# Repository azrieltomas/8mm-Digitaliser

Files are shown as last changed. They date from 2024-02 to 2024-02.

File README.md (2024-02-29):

# 8mm-Digitaliser
Hardware and software designs for the worlds worst 8mm film scanner

After finding a reel of 8mm film I set out to try to digitise it. A quick attempt with my Epson v850 showed this was not a viable option, and a stubborn refusal to look online at anyone else's attempt (for a while) led to this.

The basic design concept is to advance the film reel frame by frame, as close as possible to exactly, and photograph each frame with a digital camera.

This project consists of four parts:
* 3D printed parts for advancing the film
* Arduino microcontroller to control the stepper motor and camera
* Python script to align the images
* A few other shortcuts to turn it into a video

### Film Holder and Advancer
This is a series of 3D printed parts to hold the film in place and advance it past a lamp. To save time, I designed it without a base, and bolted each piece to a wooden board. Parts requiring a bit of accuracy were printed with a base. Partially inspired by the operation of a cassette, the film is advanced by a single sprocket, and rests on a series of rollers (or just plastic cylinders to aid alignment and tension).

The single driving sprocket was designed around the stepper motor used (a cheap-ish Jaycar YM2754 I've had sitting around for years), which steps 7.5 degrees with each movement. Given that 8mm film perforations are spaced 3.81 mm apart, the radius of the sprocket needs to be 29.106 mm. While the printer may not achieve this accuracy, the hope is any deviation causes a constant shift that can be countered later when cropping the photos.

For a lamp I used a battery powered LED lamp designed to be fitted to a camera horseshoe as kind of not-quite-ring lamp.

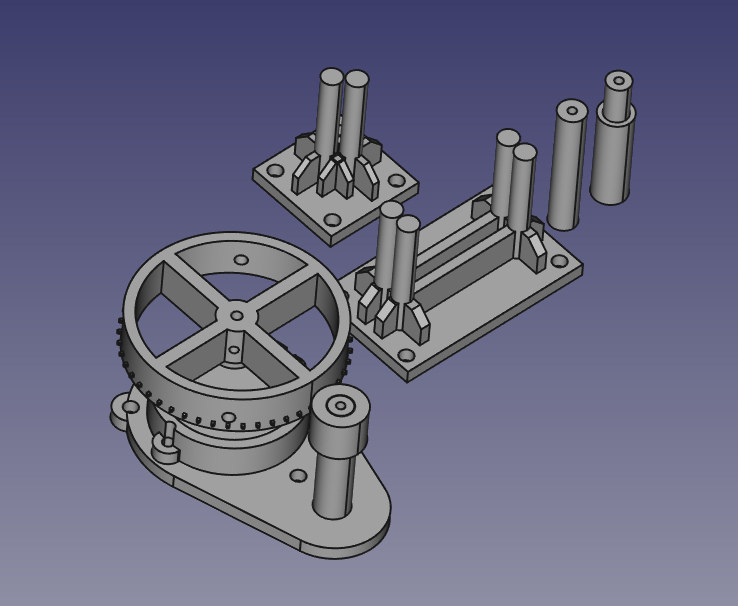
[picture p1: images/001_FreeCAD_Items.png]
3D Parts
\
*3D Parts in FreeCAD*

### Stepping and Photographing
The camera used is a Canon 200D MkII, fitted with a macro adaptor and 200 mm lens, but any camera with an external trigger and suitably powerful lens could be used.

The stepper control has four buttons: step forward, step backward, run continuously, halt. After stepping the motor, the system waits for a 250 ms for everything to settle, fires the shutter, waits 500 ms for the shutter to finish, and then another 500 ms for cooling. This last part is imperative when using 3D printed parts - the stepper motor when stopped (but enabled) dissipates 12W of heat which soon starts softening the driving sprocket and causing it to slip. Giving it half a second to cool by disabling it solves the heat problems, and keeps the noise of the bench power supply down.

The camera's trigger socket is only a 2.5 mm TRS connection:
* Tip: Shutter
* Ring: Focus
* Sleeve: Ground

By shorting T or R to S the camera will activate this function. With S connected to ground, T is "shorted" by enabling a 74HC126 tri-state buffer output. Otherwise the buffer is disabled and output in Hi-Z mode. Alternatively a 5V relay can be used.

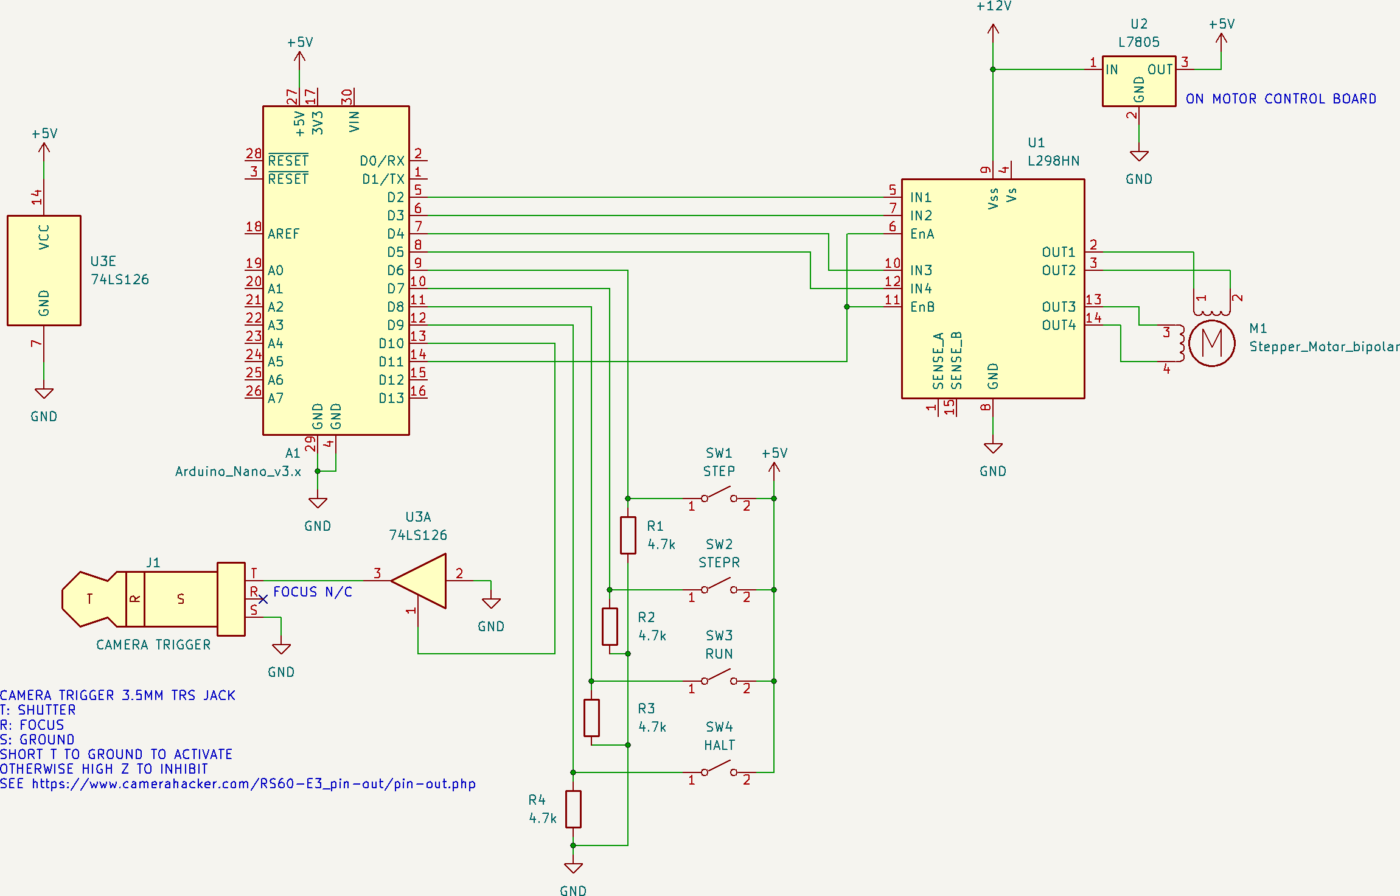
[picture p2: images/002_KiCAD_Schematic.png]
Circuit Design
\
*Circuit Design in KiCAD*

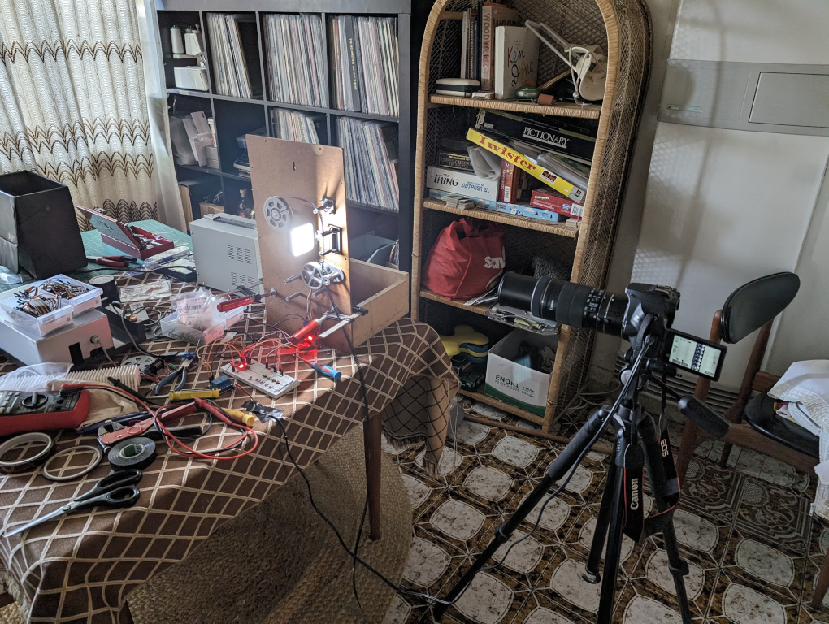
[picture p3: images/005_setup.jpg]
A mess
\
*Physical setup, experiencing continuous modification & improvement*

### Aligning Photographs
Prior to alignment, the photographs need to be cropped appropriately. I've done this either in Lightroom very quickly or by using ImageMagick (choosing a rough image size and start position):
```
for f in *.tif; do convert -crop (resx)x(resy)+(xpos)+(ypos) +repage $f crop_$f; done
```

This scanning system has a lot of bounce and shift. In an attempt to smooth it out, I tried the following to align the images:
* Hugin image stitcher (didn't really work)
* ImageJ / Fiji (didn't really work)
* Photoshop auto-align (awful results)
* Vidstab (decent results, but frame tracking starts to shift like a bad VCR)

The problem with the image programs is they're attempting to align the images in the 8mm frame, not the frame itself. For a moving camera film this is obviously not what we want.

After trying these I sought a better solution and came upon [cpixip's Super-8 detector](https://github.com/cpixip/sprocket_detection). This was a fantastic program and I could not thank them enough for their hard work (check out [their profile on Kinograph.cc](https://forums.kinograph.cc/u/cpixip/summary)), but a couple differences between Super-8 and 8mm meant this required some modification:
* Super-8 perforations are aligned with the centre of the image, 8mm is aligned with the top and bottom, meaning there are two holes per image (or rather, two halves)
* The 8mm film I have has Kodak lettering along the edge, which throws the detector at times

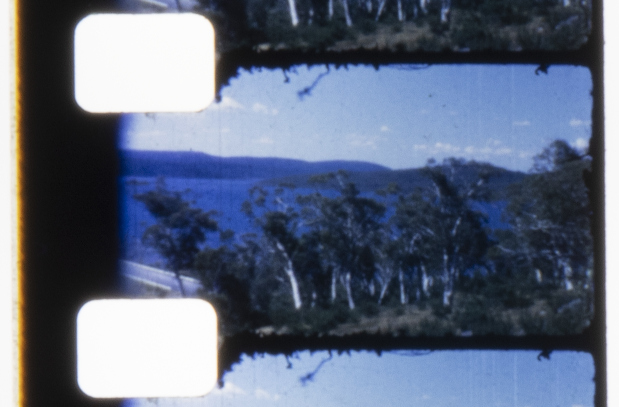
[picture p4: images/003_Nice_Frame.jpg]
A nice frame
\
*An easy frame to analyse*

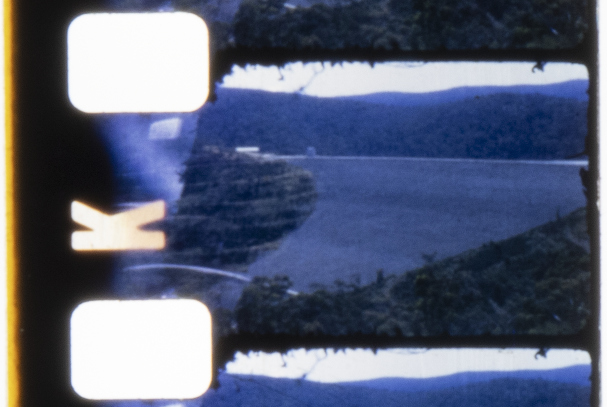
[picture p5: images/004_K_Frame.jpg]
An annoying frame
\
*A more difficult frame to analyse*

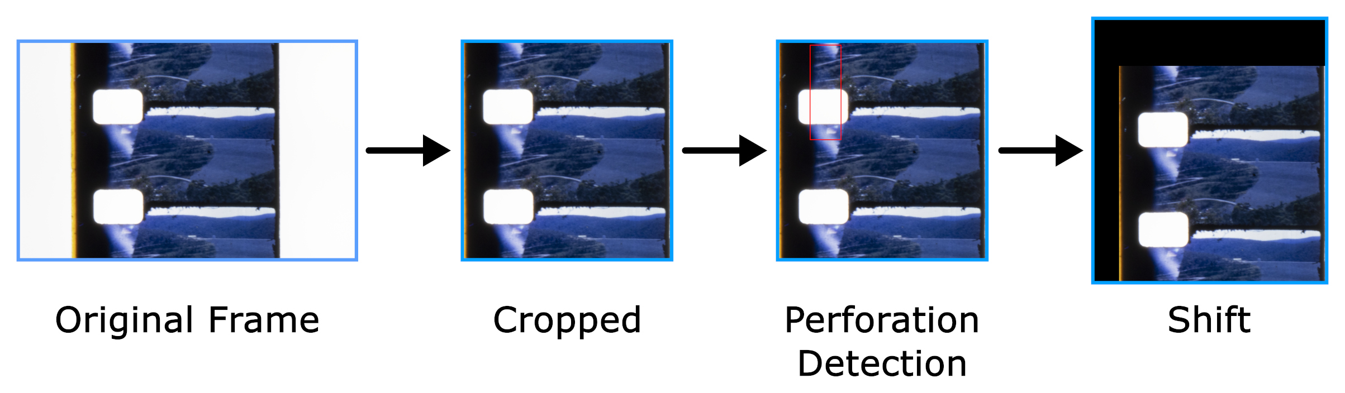
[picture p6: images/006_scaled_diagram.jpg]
Perforation detection and shifting
\
*Detecting the perforations and shifting*

I made the following changes to cpixip's code:
* Implemented a function to loop through all images in a folder of a defined type (eg jpg, tif, etc)
* Crop the additional whitespace around the image
* Flip the image if necessary (all my images were photographed backwards)
* Adjustments to the "region of interest" to align with 8mm film
* Removed the histogram smoothing (this tends to throw it off because of extra noise in the film header)
* Resizes the canvas before moving the image (the perforation offset meant the image was getting chopped off otherwise)
* Does multiple passes on images that have not been shifted (ie, no perforation detected)
* Loop through all output images and resize their canvases to match
* Debug outputs:
	* If additional passes fail to detect the perforation, it will save an image with the ROI rectangle drawn over it
	* If required, save the histogram plot (requires matplotlib)

#### Use
```
python detectSprockets.py [file format] [optional: flip]
```

eg. detect in tiffs, without flipping
```
python detectSprockets.py tiff
```

eg. detect in pngs, flip image
```
python detectSprockets.py png flip
```

### Outputting Video
Now the out_* files are created, its a trival task to combine them with ffmpeg. You can use any codec you prefer, but here's an example for a easy uncompressed x264 video at 16 fps (the standard framerate for amateur 8mm film):
```
ffmpeg -framerate 16 -pattern_type glob -i '*.tif' -c:v libx264 -qp 0 -vf "pad=ceil(iw/2)*2:ceil(ih/2)*2" -pix_fmt yuv420p output.16fps.mp4
```

Of course my video was reversed, so the output needs reversing too:
```
ffmpeg -i output.16fps.mp4 -vf reverse -c:v libx264 -qp 0 reversed.mp4
```

Additional smoothing can be done with vidstab but I found it not worth it. There are plenty of online resources available for using ffmpeg and vidstab.

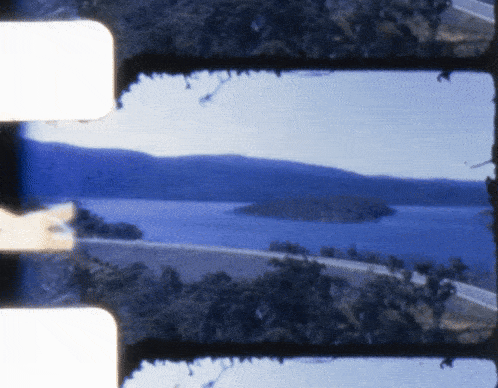
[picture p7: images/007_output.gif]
Example final output
\
*A few seconds of the final output, scaled down and trimmed and converted to a gif*

It is not a perfect solution, but it is good enough for now.

### Issues
Aside from the obvious misalignment, the whole setup suffers as below:
* Stepper motor generates too much heat and warps / softens the parts (even PETG)
* Alignment jigs only align one dimension
* Take up spool does not take up
* Camera physical parts likely to wear out
* Breadboard connections failed repeatedly

### Better Solutions
While keeping costs down, the best overall option is to fix alignment issues in hardware rather than software
* Just use an 8mm projector and modify it
* Use a better stepper motor
* Use a regular motor (with a few gear shifts to keep it turning slow) and an IR sensor to halt movement when the perforation passes it
* Alternatively, the right shutter speeds and slow movement could keep the system turning continuously, with the sensor triggering the camera only

Additional hardware changes that could be made:
* Use a mirrorless camera, not a DSLR
* Solder the controller
* 3D print a better alignment jig
* Implement sound capture with magnetic tape head (where required)

### Future
With no more 8mm films to digitise, the better solutions are being implemented in the [16mm Digitialiser](https://github.com/azrieltomas/16mm-Digitaliser)

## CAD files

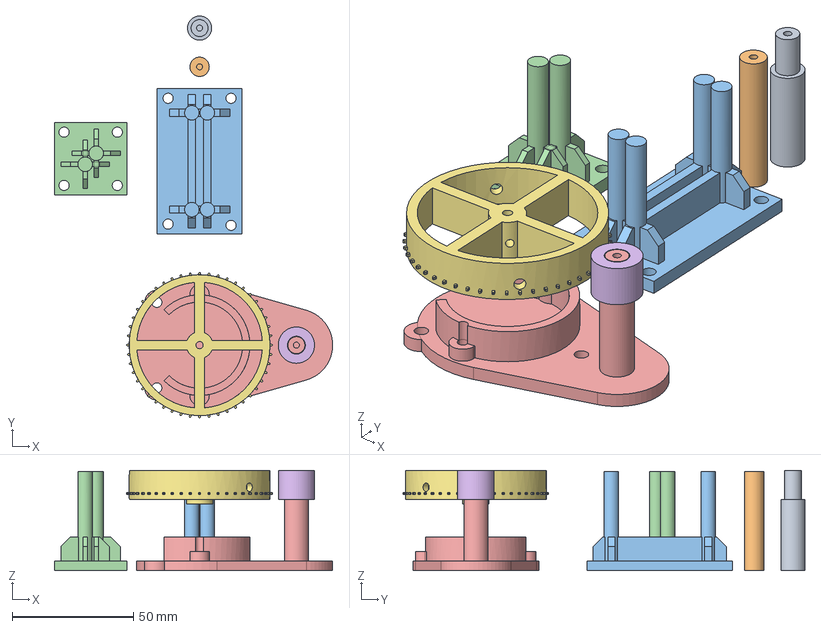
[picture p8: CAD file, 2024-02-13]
Digitaliser Rig V2-Parts.FCStd
115.0 x 166.1 x 41.5 mm
ReelStand
TensionerSingle
TensionerGroup
TensionerPair
MotorAndRoller
FilmRoller
FilmDriver

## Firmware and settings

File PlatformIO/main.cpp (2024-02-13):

#include <Arduino.h>
#include <Stepper.h>
#include "DebugUtils.h"

// timing doesnt need to be exact here
// use digitalRead/Write and delay
// allow at least one second per frame total for motor stepping & camera operation

#define DEBUG           0

#define STEP1_PIN       2   // MOTOR A1
#define STEP2_PIN       3   // MOTOR A2
#define STEP3_PIN       4   // MOTOR B1
#define STEP4_PIN       5   // MOTOR B2
#define STEP_FWD_PIN    6   // SWITCH - STEP MOTOR FORWARD
#define STEP_REV_PIN    7   // SWITCH - STEP MOTOR BACK
#define STEP_RUN_PIN    8   // SWITCH - MOTOR CONTINUOUS RUN
#define STEP_HALT_PIN   9   // SWITCH - STOP MOTOR
#define BUFFR_ON_PIN    10  // ACTIVE HIGH - TRIGGERS CAMERA BY ENABLING 74LS126
#define STEP_ENABLE     11  // ENABLE MOTOR - use one pin for both enables
#define LED_INT_PIN     13  // INTERNAL LED for indication

#define SHORT_DELAY     250
#define LONG_DELAY      500

// constants
const uint8_t STEPS_PER_REV = 48; // steps per motor revolution
const uint32_t DEBOUNCE_TIME = 250; // debounce timing for buttons (ms)

// timers for switches
uint32_t timerFwdSwitch = 0;
uint32_t timerRevSwitch = 0;
uint32_t timerRunSwitch = 0;
uint32_t timerHaltSwitch = 0;
bool systemRunning = false; // control system for halt / run modes

// set up stepper motor control
Stepper motorStepper(STEPS_PER_REV, STEP1_PIN, STEP2_PIN, STEP3_PIN, STEP4_PIN);

void stepMotor(int stepAmount) {
    digitalWrite(STEP_ENABLE, HIGH);    // enable motor
    delay(10);                          // wait for signal to propagate

    motorStepper.step(stepAmount);      // step motor
    DEBUG_PRINT("Motor stepped", NULL);
    delay(SHORT_DELAY);                 // wait for stabilisation

    digitalWrite(BUFFR_ON_PIN, HIGH);   // camera trigger & LED on
    digitalWrite(LED_INT_PIN, HIGH);

    delay(LONG_DELAY);                 // wait to allow shutter to operate

    digitalWrite(BUFFR_ON_PIN, LOW);    // camera trigger & LED off
    digitalWrite(LED_INT_PIN, LOW);
    
    digitalWrite(STEP_ENABLE, LOW);     // disable motor when not in use to reduce power (and heat)
    delay(LONG_DELAY);                  // wait to allow camera to process
}

void setup() {
    if (DEBUG) {
        Serial.begin(9600);
    }

    // pin setups
    pinMode(STEP_FWD_PIN, INPUT);
    pinMode(STEP_REV_PIN, INPUT);
    pinMode(STEP_RUN_PIN, INPUT);
    pinMode(STEP_HALT_PIN, INPUT);
    pinMode(BUFFR_ON_PIN, OUTPUT);
    pinMode(STEP_ENABLE, OUTPUT);
    pinMode(LED_INT_PIN, OUTPUT);

    digitalWrite(BUFFR_ON_PIN, LOW); // initial state with trigger off
    digitalWrite(STEP_ENABLE, LOW); // initial state with motor off
    digitalWrite(LED_INT_PIN, LOW); // initial state with LED off
}

void loop() {
    // read switch states
    uint8_t fwdPinState = digitalRead(STEP_FWD_PIN);
    uint8_t revPinState = digitalRead(STEP_REV_PIN);
    uint8_t runPinState = digitalRead(STEP_RUN_PIN);
    uint8_t haltPinState = digitalRead(STEP_HALT_PIN);

    DEBUG_PRINT("fwdPinState", fwdPinState);
    DEBUG_PRINT("revPinState", revPinState);
    DEBUG_PRINT("runPinState", runPinState);
    DEBUG_PRINT("haltPinState", haltPinState);
    DEBUG_PRINT("systemRunning", systemRunning);

    // handle switch with timer for pseudo-debouncing
    if ((timerFwdSwitch == 0) & (fwdPinState == HIGH)) {
        timerFwdSwitch = millis();
    }
    if ((timerRevSwitch == 0) & (revPinState == HIGH)) {
        timerRevSwitch = millis();
    }
    if ((timerRunSwitch == 0) & (runPinState == HIGH)) {
        timerRunSwitch = millis();
    }
    if ((timerHaltSwitch == 0) & (haltPinState == HIGH)) {
        timerHaltSwitch = millis();
    }

    if (!systemRunning) {
        system in standby mode waiting for input
        if ((timerFwdSwitch > 0) && ((millis() - timerFwdSwitch) > DEBOUNCE_TIME)) {
            stepMotor(1); // step motor forward once
            timerFwdSwitch = 0; // reset
        }
        if ((timerRevSwitch > 0) && ((millis() - timerRevSwitch) > DEBOUNCE_TIME)) {
            stepMotor(-1); // step motor backwards once
            timerRevSwitch = 0; // reset
        }
        if ((timerRunSwitch > 0) && ((millis() - timerRunSwitch) > DEBOUNCE_TIME)) {
            // set autorun mode
            systemRunning = true;
            timerRunSwitch = 0; // reset
        }
    } else {
        // system is in run mode
        if ((timerHaltSwitch > 0) && ((millis() - timerHaltSwitch) > DEBOUNCE_TIME)) {
            // halt system
            systemRunning = false;
            timerHaltSwitch = 0; // reset
        }
    }

    // step motor if system is in run mode
    // run this code outside of the above statement because the above can change the state
    // this will be called continuously until halted by the user
    // the delay built into stepMotor() will stop this from occuring too fast
    if (systemRunning) {
        stepMotor(1);
    }

    // outputting serial lines - pause to allow reading
    if (DEBUG) {
        delay(1000);
    }

}

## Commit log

2024-02-12 arduino control
    [Digitaliser KiCAD-backups.kicad_sch, Digitaliser KiCAD.kicad_pcb, Digitaliser KiCAD.kicad_sch]
2024-02-18 sprocket detect
